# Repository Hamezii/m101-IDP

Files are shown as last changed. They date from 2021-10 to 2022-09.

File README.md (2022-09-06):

# CUED Integrated Design Project

- Integrated Design Project Project (10/2021 – 11/2021, 2 months)
- Robotics challenge organised by Cambridge University Engineering Department (CUED). The goal is to differentiate pure plastic blocks (blue) and blocks containing metal (red), then deliver the blocks to certain area (red and blue square areas).
- Our robot completed tasks and achieved 4th place among all 13 teams

<br>
Team name: TAIPEI101<br>

Team member:<br>
| name | Role |
| --- | --- |
| Derek Dong | Elec engineer, team leader |
| Laura Clapham | Elec engineer |
| Caleb	Chan | ME engineer|
| Ben Silva | ME engineer|
| Tom	Hill | Algorithm engineer|
| James	Lecomte | Algorithm engineer|

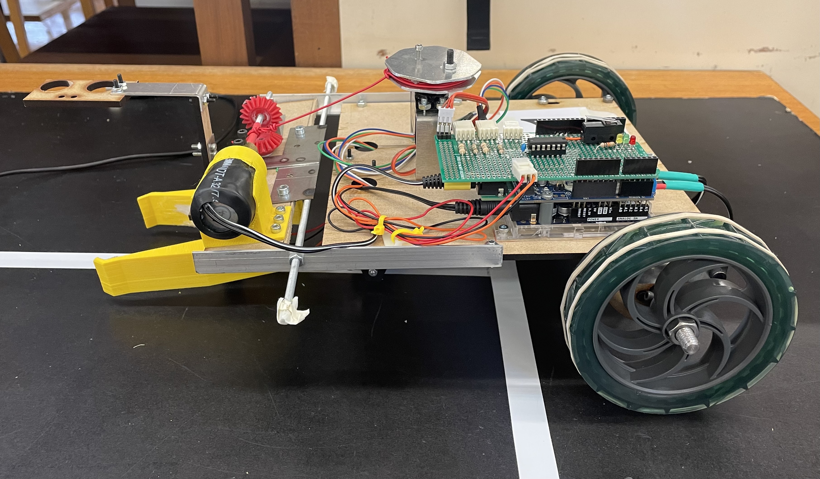
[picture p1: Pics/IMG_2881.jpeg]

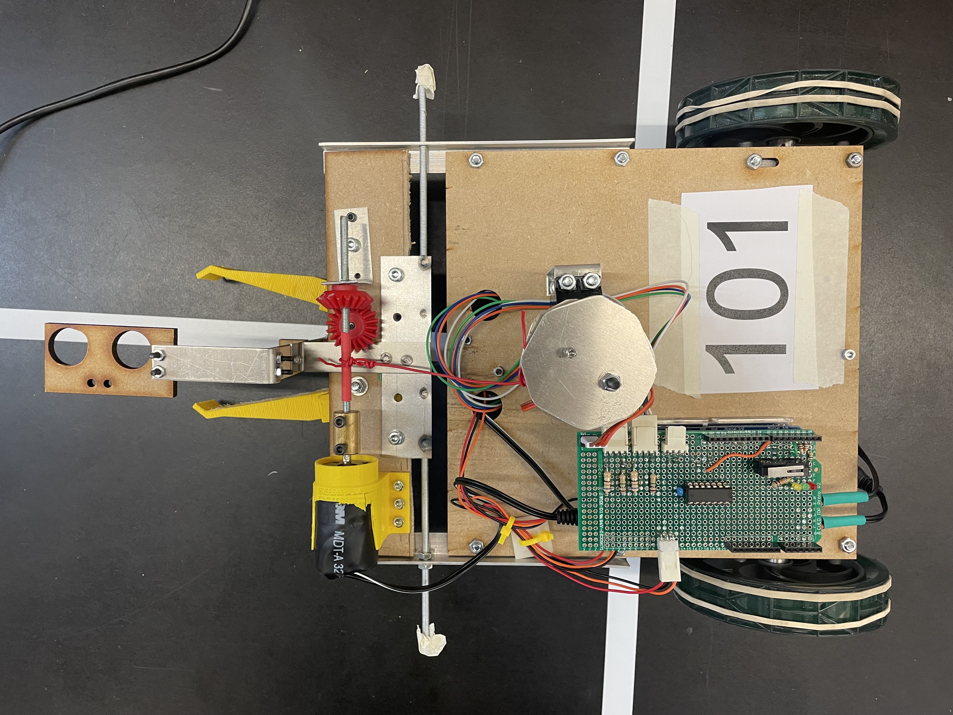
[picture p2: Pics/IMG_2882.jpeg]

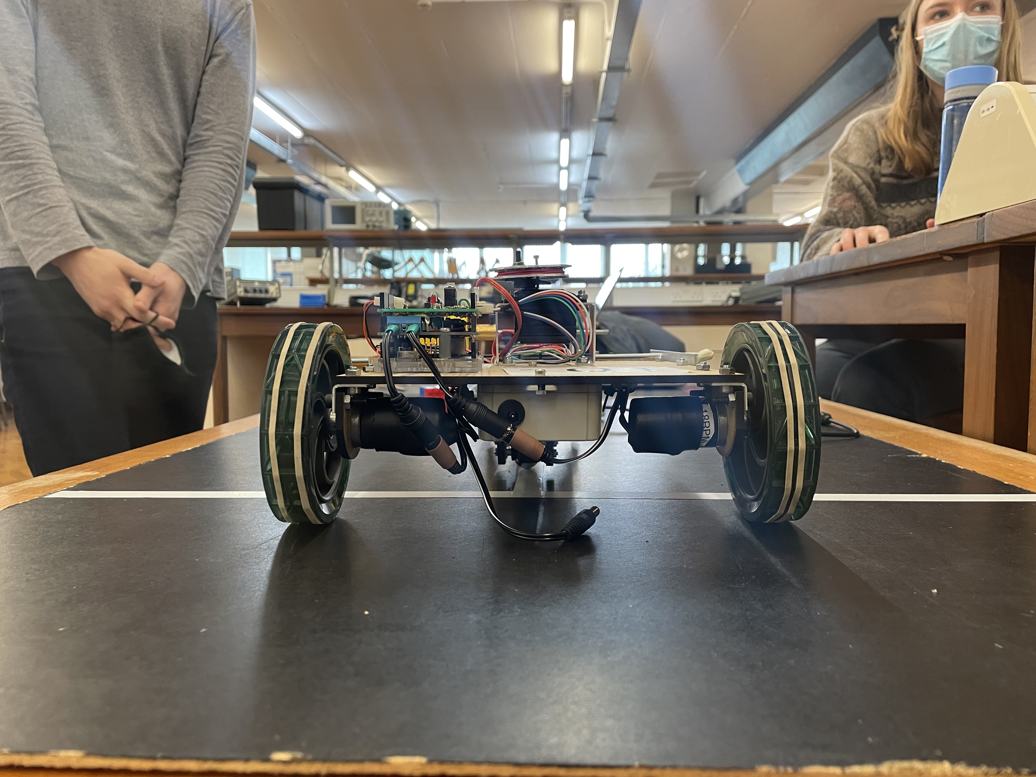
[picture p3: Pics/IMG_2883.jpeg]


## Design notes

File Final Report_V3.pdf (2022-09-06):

IDP REPORT – M101 | 1

### Department of Engineering

# TAIPEI 101 (M101)

# Final Report

Name | Crsid | Lab group
Laura S. Clapham | lsc43 | 43EM
Ben L.C. Silva | blcs2
Caleb C.C. Chan | cccc4 | 44EM
Tom Hill | th621
Derek J. Dong | jd976 | 45EM
James C-C. Lecomte | jccl4

### I. Outline

Design details

1. Overall Design Approach
2. Mechanics
a. Initial design of front section
b. Initial design of main chassis
c. Problems encountered and changes made after integrating
d. Driving
3. Electronics
a. Approach to design and testing
b. Metal Detection
c. Pathing (Line follower)
d. Block searching
4. Software

Reflections

1. Team Structure Review
2. Team Efficiency Review
3. Pathing & Block Searching Mechanism Review
4. Metal Detection system Review
5. Competitions Performance Review
a. Failure of 1st competition
b. Performance in final competition

Appendix

### II. Design details

### 1. Overall Design Approach

Our approach for the robot was to navigate to the collection zone using the line sensor, find the block using either the infrared distance sensor or ultrasound, clamp it in motorised arms, and then detect metal using a metal detector with a fixed position relative to the arms. We chose to use the line sensors as we thought computer vision was too difficult to implement in the time scale. This proved to be a good decision as one of our software team members fell ill and was forced to leave Cambridge, which would have made computer vision significantly harder to integrate.

We chose to use sensors to locate the block as we thought it would be more reliable than a mechanical system that attempted to sweep the entire collection zone at once. However, there was a lot of noise in the sensor signals which proved difficult to resolve and delayed the creation of a detection algorithm. This ultimately led to a redesign of our scanning process which was not fully implemented by the time of the competition. It is possible that by choosing a purely mechanical solution, we could have reduced the time needed to test and integrate, and therefore have been ready by the competition deadline. Our choice of arms was successfully implemented however, which provided good clearance over the ramp by elevating the block.

We decided to use a metal detector vs picking up the block with a magnet as we were unaware of the magnet’s availability during the initial planning stage, and when it became available, we did not stop to reconsider our previous choice. To ease integration with other components, we decided on a state-based program that was entirely modular. This eliminated the risk of a change effecting other parts of the program and was the right decision to make for a large project. However, it did make it slightly difficult for team members who had not encountered a state-based system to help check the code in the later stages of the project.

[Appendix D1: Whole system block diagram]

### 2. Mechanics

Initial design of front section

At first glance, we thought of hooping and dragging the block from the collection area back to the deliver area, as a less complicated mechanism would be required. However, when we inspected the competition table, we discovered that there is a small discontinuity going from the table surface to the ramp which might prevent the block being dragged over. [appendix M1] Therefore, we decided to lift the block to provide clearance above the ramp. To do this, we need a front section composing of the grabbing components which can be raised and lowered by a servo motor. We need a servo motor for this purpose because it can lock its position in order to keep the front section lifted. A spool of wire was constructed out of steel sheets and mdf, with the steel filed down to be roughly circular. We decided water jetting a steel circle was unnecessary and too slow.

Mounted on the front section is an 18 RPM motor, two grabber arms and a worm gear. After some prototyping with cardboard, we discovered turning one notch on the arm gears would require one full worm rotation. Turning 6 notches to close the arms would take 20 seconds with the 18 RPM motor which we decided is too slow. As a result, the worm gear is replaced with two helical gears which opens and closes within 1 second.

The main platform of the front section is 4mm MDF board laser cut to 200mm x 8mm. The brackets for the helical gears are made from steel sheets, and the front section is connected to the main section by a steel plate spot-welded to a studding and bolted to the front section. The arms were prototyped in bent steel, and later changed to 3D printed.

Initial design of main chassis [appendix M2: CAD of Robot] [appendix M3: Picture of Robot]

As the arms will continuously grab the block and be lifted until the robot reaches the collection area, there is no need for a place on the chassis to store the block. Therefore, in order to keep manufacturing process as simple as possible and high accessibility to components, we went with a flat platform design. The chassis is made of 4mm MDF sheet laser cut to 200mm x 200mm.

We discovered it would be difficult to steer the robot using 4 wheels. Therefore, we decided to use a 3-wheel system, with two motorised wheels and a ball caster as the third support. This allows us to steer the robot by just giving the motors different angular velocity and let the ball caster swing left and right. The 4” wheels are chosen for two reasons: a) to maximise speed (40RPM x 4” x π = 12.8 m/min and b) to keep the chassis high off the ground enough so it does not get stuck on the edge of the ramp and the bridge. Although this raises the centre of mass, which could affect stability, we decided to go ahead as we believe our wheelbase is long enough to prevent the robot from tipping over. The ball caster is mounted onto the chassis with a long arm in order to keep the chassis levelled.

The servo motor is mounted on the main chassis, and it would pull a string attached to the front section, which would be pivoted against the front of the main chassis. Shelves are placed at the rear of the chassis to place the Arduino boards and circuit boards. The battery is mounted towards the rear of the chassis on the underside to offset the moment created by the front section and maximise space for electronics. Most of the mounts will be fabricated by bending aluminium sheets into the right shapes. The motor mount was originally 3D printed. However, given the wire heat-shrinked onto the motor casing gives it a lot of irregularities, the 3D printed mount could not grip the motor properly. So, we switched to using a MDF board cut-out which is mounted to the screw plate of the motor and the main chassis though an aluminium angle.

Problems encountered and changes made after integrating

When we first assembled the robot and tested the line following algorithm, we discovered some major problems.

First, due to wear and tear of the motors from previous years, the power and torque output by the 40RPM motors are not balanced, meaning 1 side of the robot has more driving force acting on it than the other side, causing the robot to always drift. The bigger problem is that the side with less power could not climb up the ramp, causing the robot to rotate up the ramp. To solve this, we switched out the 40RPM motors for 18RPM motors which are in slightly better condition and capable of producing more torque. As expected, the change turns out to be the right one.

With the 18RPM motor switched out, we had to use the 40RPM motor to drive the grabber arms, which caused the second problem. The 40RPM motor does not produce enough torque for the grabber arm to grip the block firm enough. As a result, we had to put something on the surface of the grabber arm to increase friction. We have tried sandpaper, heat shrink and rubber bands, at the end we went with spreading an even layer of hot-melt adhesive on the surface. Although it is not an elegant solution, it gives us just enough grip to transport the block.

As we were testing the line following algorithm, it was discovered that the robot was slightly understeering. This caused issues in line detection and pathing, as the algorithms worked off the assumption that the point of rotation lied on the driving wheel axes. To fix this we shorten the front section to bring the centre of mass towards the rear to allow easier steering.

### 3. Electronics

[Appendix E1: Overall schematic diagram] & [Appendix E2: Overall layout]

Approach to design and testing

There were three main tasks for the electronics team: metal detection, line following and block searching. Originally, we split tasks among the team and worked on them separately. This approach had its advantages, like easily being able to work on the project at home and getting two tasks done at once, but eventually we realised that it was more effective to work together on the same task. This meant we could use different perspectives and ensure that each other moved on when something wasn’t working instead of obsessing over the same strategy.

The three main tasks remained almost completely isolated from each other throughout the project meaning we could easily ensure that each aspect was working properly before we used them all together. LT Spice was used to model behaviour of systems and to optimise values of components and the output signals were measured using a PicoScope and the Arduino.

The electronics team had to work with the mechanics and software teams closely. For example, the design of the metal detector affected its location on the robot and whether it would have to move up and down using a servo. The output of the metal detector had to be interpreted and processed by the software team. A rolling average algorithm was used to clean the signal and the result taken by the metal detector would have to change the state of the robot.

Metal detection

The metal detector uses an AD22151 magnetic field sensor that contains a hall effect sensor and amplifier circuit. It gives out a high voltage when the magnetic field strength is over a certain value and otherwise a low voltage. A magnet is placed above the sensor at a distance that gives a low value when there is no metal in between it and the sensor but a high value when the block is placed on top of the sensor. The circuit was soldered onto its own board and placed in between the grabber arms. As the robot drove up to the block, the block would be pushed onto the breakout board containing a hall effect sensor.

The magnetic field sensor was a late revelation as the solution for the vast majority of the project was to use a coil. The circuit would have used the fact that the inductance of a coil increases when in the presence of ferrous metal. The inductor was used in a tank circuit with a capacitor. When the inductance increases the charge collected on the capacitor, and so the voltage over the capacitor, increased and could be measured. The reason this was changed is explained in the reflections section.

Pathing (Line follower)

For pathing, we wanted to allow the robot to be aware of its position on the table, and to do so we want line sensors to detect lines. We want the robot to be able to follow lines and detect perpendicular lines it comes across, so we designed a system to satisfy both criteria. We put two line-sensors on the front of the robot since it is the minimum amount needed to gather enough information.

The line follower circuit includes an OPB704 line sensor which uses an LED, emitting IR light, and a phototransistor. When on the line a low voltage is output and when off the line a high voltage is output. This signal enters a SN7414N Hex Schmitt inverter before being input to the Arduino for use in the line following program.

The accurate position of two sensors were carefully considered. The main problem was that the distance between sensors and the ground changed when the robot going up or down on the ramp, and line sensors only work in a certain range of distance. We managed to find out that the rear of the front wheel is a good position, and specific distance was determined by several experiments.

Block searching

The final plan was to mount the ultrasonic sensor in front of the robot facing downwards and for the robot to scan the entire box by rotating to scan the entire width then moving forward and scanning the next width and so on. The failure of this aspect is explored further in the reflections section.

### 4. Software

[Appendix S1: Flowchart of software]

The basic of our software design is state-driven: we used Finite State Machine to determine robot behaviour
s. All sensor inputs are converted to a rolling average to decrease the noise.

Pathing algorithm is based on 2 line sensors. Data from the line sensor is used to correct the direction of the robot by changing the velocity of the left and right wheel motors separately in a negative feedback loop. When one sensor circuit detected a white line the robot would know that its path was deviating too far to the other side and so it would turn in the opposite direction until this was corrected.

The program could remember when a horizontal line was crossed (detected when Arduino receives high signals from both sensor circuits). This allowed the robot to know which state to enter at which time, for example it would know when it had reached the collection box and so would know when to start the grabbing cycle.

### III. Reflections

### 1. Team Structure Review

Our team have one team leader and 3 sub-teams (ME, Elec, Software). We used Slack to communicate, GitHub to share progress and Gantt chart to track deadlines.

3 sub-teams structure can make sure that every member has a clear role, which is quite manageable and normally increases team productivity. However, in a small project like IDP, some drawbacks are shown. First, this structure reduces communication between sub-teams, which means lack of information flow. For example, some of our team members did not know much about software designs. Before the first competition, all the members who knew how the software works happened to be absent until 2 minutes before the competition, and the three remaining members couldn’t even start the robots. This resulted in us not having time to test the robot before the competition and thus failing in it. Second, it also leads to some under-utilisation of human resources (e.g. the software cannot be tested until the overall robot has been built). Potential improvement includes having more team meeting to help communicate and educating other sub-teams on how stuff works to allow them to know the overall graph.

Having a clear team leader can lead to a high team productivity and can ensure the decisiveness of the team in case of disagreement. However, the advantages highly depend on the leader: When the leader is not good at managing or cannot devote sufficient effort to managing, the team productivity decreases dramatically (this happened in the project).

### 2. Team Efficiency Review

From the team leader’s point of view, the team M101 has good productivity, but it can still be improved by several measures:

- Avoid schedule mistakes (e.g. Dyson centre opening hours)
- Set specific tasks for each lab session instead of setting a vague goal of “do this by that time”. For each phase rather than talking about what to do in general (e.g. set a deadline as “implement line-following before 16 Oct” “finish final chassis cut and start to build final circuit on it before 2 Nov” instead of “we should finish all designs before 10 Oct” “We should combine all parts to get a complete robot before 15 Oct”. They can be good guidelines but not suitable deadlines.
- Consider team focus carefully. Vital tasks should be figured out and focused on in advance so that team productivity can be fully used to gain the most benefits.
- Report progress to teach other sub teams about how to get your finished work integrated so when some member becomes unavailable during the project (which happened to us), other sub team members can substitute and help with balancing workload.

### 3. Pathing & Block Searching Mechanism Review

Computer vision & line-following

Computer vision was seriously considered along with line-following as path-designing method at the beginning of the project. We considered it as a powerful tool but decided that this would not be necessary, since using it would be an over-engineered solution that has many failure points and would take too long to develop and is likely to be unreliable. It is too dependent on factors like the brightness level of the room and shadows cast on the table, etc.

Block searching

Implementing a block searching mechanism was the most challenging aspect of the project; there were many issues with the distance sensors that were not apparent at the start. When the block surface is not directly normal to the sensor the readings given are inaccurate and inconsistent. Therefore, the original design where an ultrasonic sensor would be placed at the front of the robot facing horizontally was problematic. Mounting the ultrasonic sensor on an antenna-like structure so that it points down solved this issue. This unfortunately was only sorted late into the project so it was difficult for the software team, who were often unable to attend, to code a way for the robot to scan the box. It became apparent that it was going to be almost impossible to finish the block finding system in time for the final competition so we had to make the decision to leave it out and focus on other things so we could at least secure 30 points.

Metal detection system review

One of the biggest major changes in the design of the robot was the switch from a inductor coil-based system to detect metal to a hall effect sensor at 3 weeks into the project. This was the correct decision to make as previous detectors using the coil were extremely noisy and unreliable, however it was a difficult decision to make as considerable amounts of time had been spent trying to make them work. With hindsight the decision should have been made a long time before but the small advances with the detector coils made it seem as though a breakthrough was always near. The main problems with using the coils were that they were insensitive and so struggled to detect the small amount of steel within the block. It was also time consuming to make different coils to test and optimize the components used in the circuit.

Competition's performance review

- Failure of 1st competition

Our expectation before the 1st competition was to reach the other side but not to collect or sort block. The robot had been capable of achieving this for several days, but the day before the competition we integrated the grabbing section onto the main chassis. We found in testing that this made the robot too heavy to climb up the ramp, so we knew that the front section needed to be removed for the competition. This meant it was impossible to pick up a block, but possible to cross the ramp.

However, during our testing of the robot, it seems that the left motor axle had come loose from the casing. This was likely due to a combination of historic wear and tear, and stressing the motor by having too heavy a weight for its torque limit. As a result, during the competition, in a configuration that had previously worked, the robot was unable to climb the ramp. It veered to the left and either ran off the ramp or toppled over. We had not been able to test the robot immediately before the competition, as only 3 members had arrived in time to test it, and none of them knew how the software operated. This revealed a flaw in our team management that we sought to improve before the final competition.

Coming out of the competition we had several priorities: to reduce the weight to torque ratio to an acceptable level, and to integrate the metal detector and detection algorithm. We solved the weight problem by swapping the motors as detailed in the mechanical section. We also ensured for the final competition that more people had a basic understanding of the software, and that we stopped working on the robot in plenty of time before the competition, in a state that we could test and see work.

- Performance in final competition

The day before the competition we had tested all the mechanical and electrical systems working together and all that was left to do was to integrate the software to create a scanning cycle to locate blocks. Our minimum expectation was that we could pick up the first block, as it would be placed in the same place every time, and we were hoping to be able to locate other blocks using the cycle.

However, on the day of the competition, our software team was not able to attend until an hour and a half before the competition. As more of the team had knowledge of the software vs the first competition, we were still able to test the robot and debug the code, but we were unable to create the new software needed for the scanning cycle. Therefore, we were unable to achieve more than our minimum expectation.

We did quite well in the final competition and the performance was exactly what we expected before competition: our robot managed to get the first block and correctly told the difference between metal and plastic. Compared with the first competition, our strategies changed: We still did R&D on the morning before the final competition, but each progress made was archived and ensured that it could be easily replicated. With an hour to go, we stopped development to concentrate on the competition and ensure a consistent, predictable performance in the competition.

### Appendix

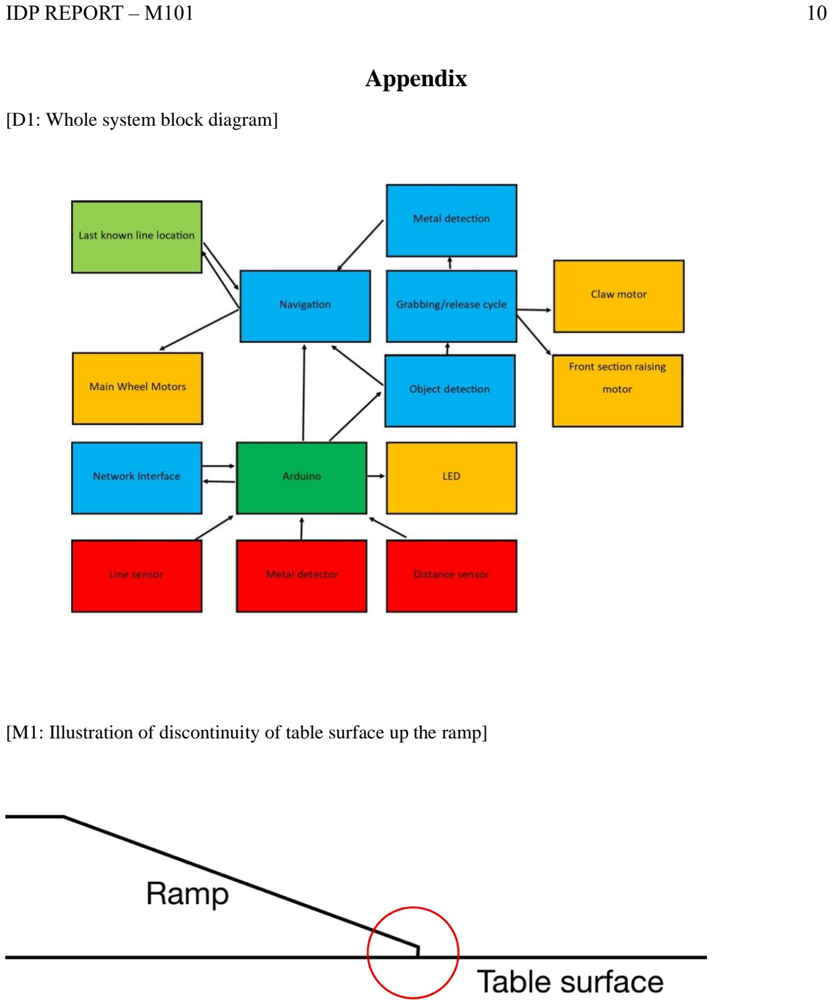
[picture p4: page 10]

[D1: Whole system block diagram]

[M1: Illustration of discontinuity of table surface up the ramp]

[M2: CAD of robot]

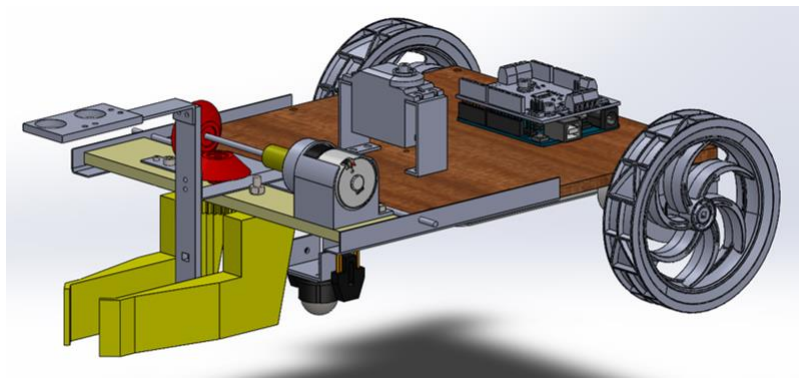
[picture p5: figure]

[M3: Assembled Robot]

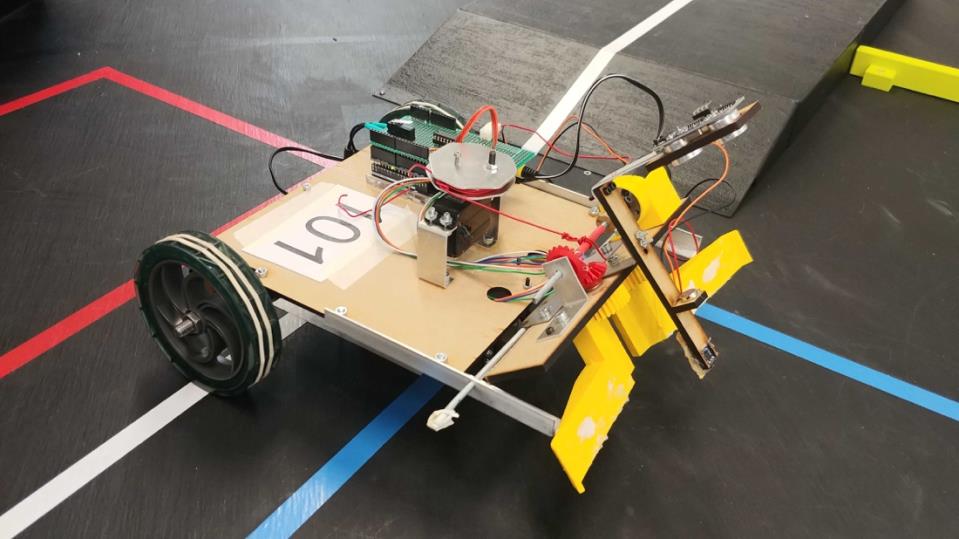
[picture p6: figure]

[M4: Torque

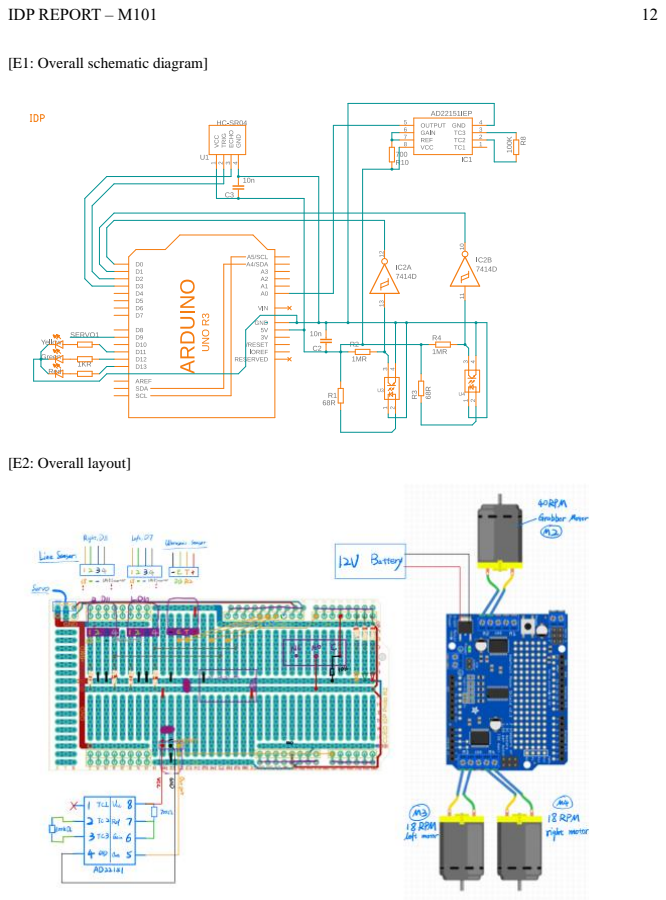
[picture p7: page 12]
[E2: Overall layout]

[E1: Overall schematic diagram]

IDP REPORT

– M101 | 13

[S1: Flowchart of software

]

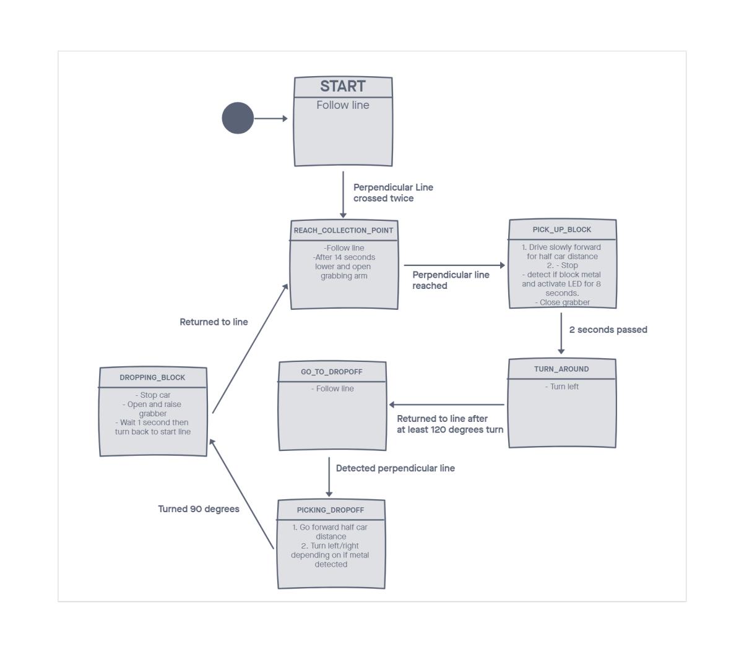
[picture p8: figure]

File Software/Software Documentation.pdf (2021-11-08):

# Software Documentation

James Lecomte jccl4 + Tom Hill th621

## CODE

Permalink to Github repo:

https://github.com/Hamezii/m101-IDP/blob/80b2492b2193943c890ced5abd1d3d18f783d01f/Software/IDPmain/IDPmain.ino

## STRATEGY

ALGORITHM AND STATE
For the robot to keep track of its location and its current place in its behaviour algorithm, we implemented a Finite State Machine into the program. This allowed us to explicitly separate the robot behaviour during the different stages of execution into their own state. This also allowed easy

## EXECUTION

SYSTEM DIAGRAM

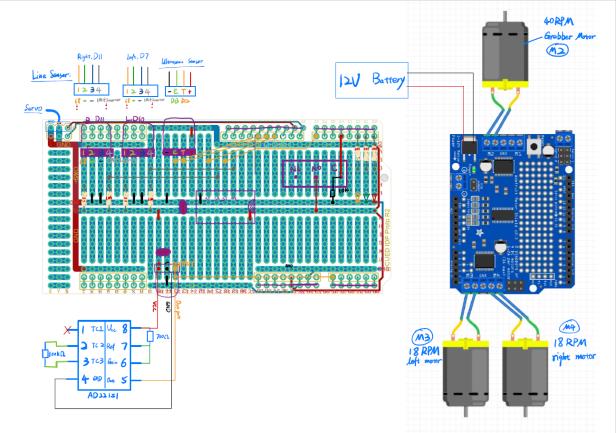
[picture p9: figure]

MAIN STRUCTURE
The program consists of subroutines organised using a state machine that enable navigation with line following, object detection with the ultrasonic sensor, metal detection, object grabbing and lifting, placing objects into the appropriate boxes, etc.

The behaviour of the robot at any given time is driven by the FSM; at any arbitrary time-step, using a combination of current state and inputs into the Arduino, the robot will modify its state and behaviour, calling subroutines to do so.

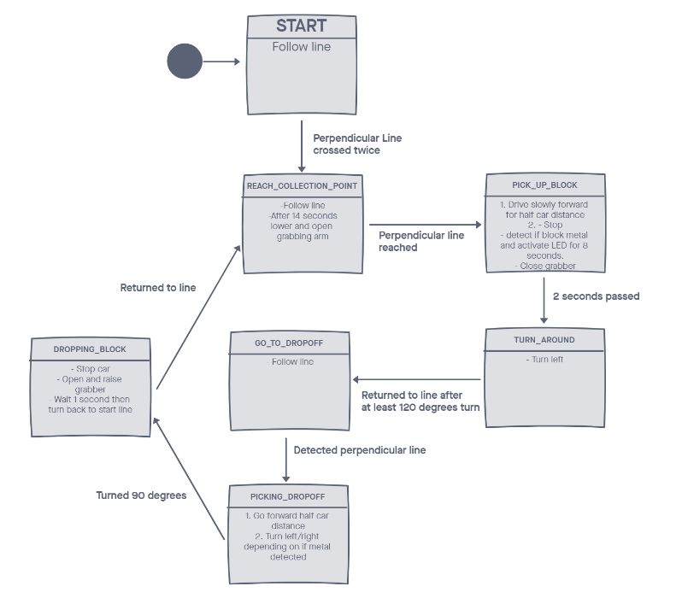
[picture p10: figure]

2

STATE DIAGRAM

PARALLEL PROCESSES
We wanted to allow continuous robot output behaviour and state management in parallel with continuous sensor readings (for running averages, see below). To do this we made sure subroutines don’t block the execution of the program by running for a non-trivial period, for example by using delays in a for loop for a continuous motion, as this essentially blinds the robot during its execution. The FSMcentric design allowed for continuous behaviour over multiple program cycles.

DETECTING PERPENDICULAR LINES
When following a line, if both line sensors read high it can be assumed that the robot has crossed onto a line perpendicular to its direction of movement. In practice, this can be used to detect an edge of the different boxed zones on the table, as well as the point at which two lines intersect.

SENSING
To ensure accurate readings from the different sensors on the robot, we made sure to eliminate noise and false readings by implementing a running average for each sensor. We read the value of each sensor every program loop and pushed it into a Queue-like RunningAverage abstract data type, taking the average of the values in the queue when polling sensors for conditional logic.

Using trial-and-error, we found that a good value for size of the running average Queues was 4, as too small would allow a single noisy reading to disrupt the mean reading and too large would cause the robot to respond too slowly to large discontinuous changes in read value i.e. when line sensors pass over a line.

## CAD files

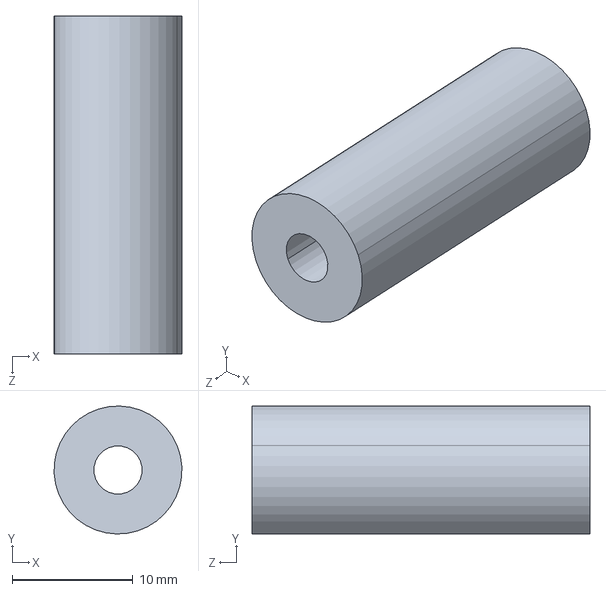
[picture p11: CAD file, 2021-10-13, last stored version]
ME/Gear Drive.SLDASM
10.6 x 10.6 x 28.0 mm

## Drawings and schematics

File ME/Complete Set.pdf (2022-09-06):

13 | 11 | 12 | 2 | 19

23

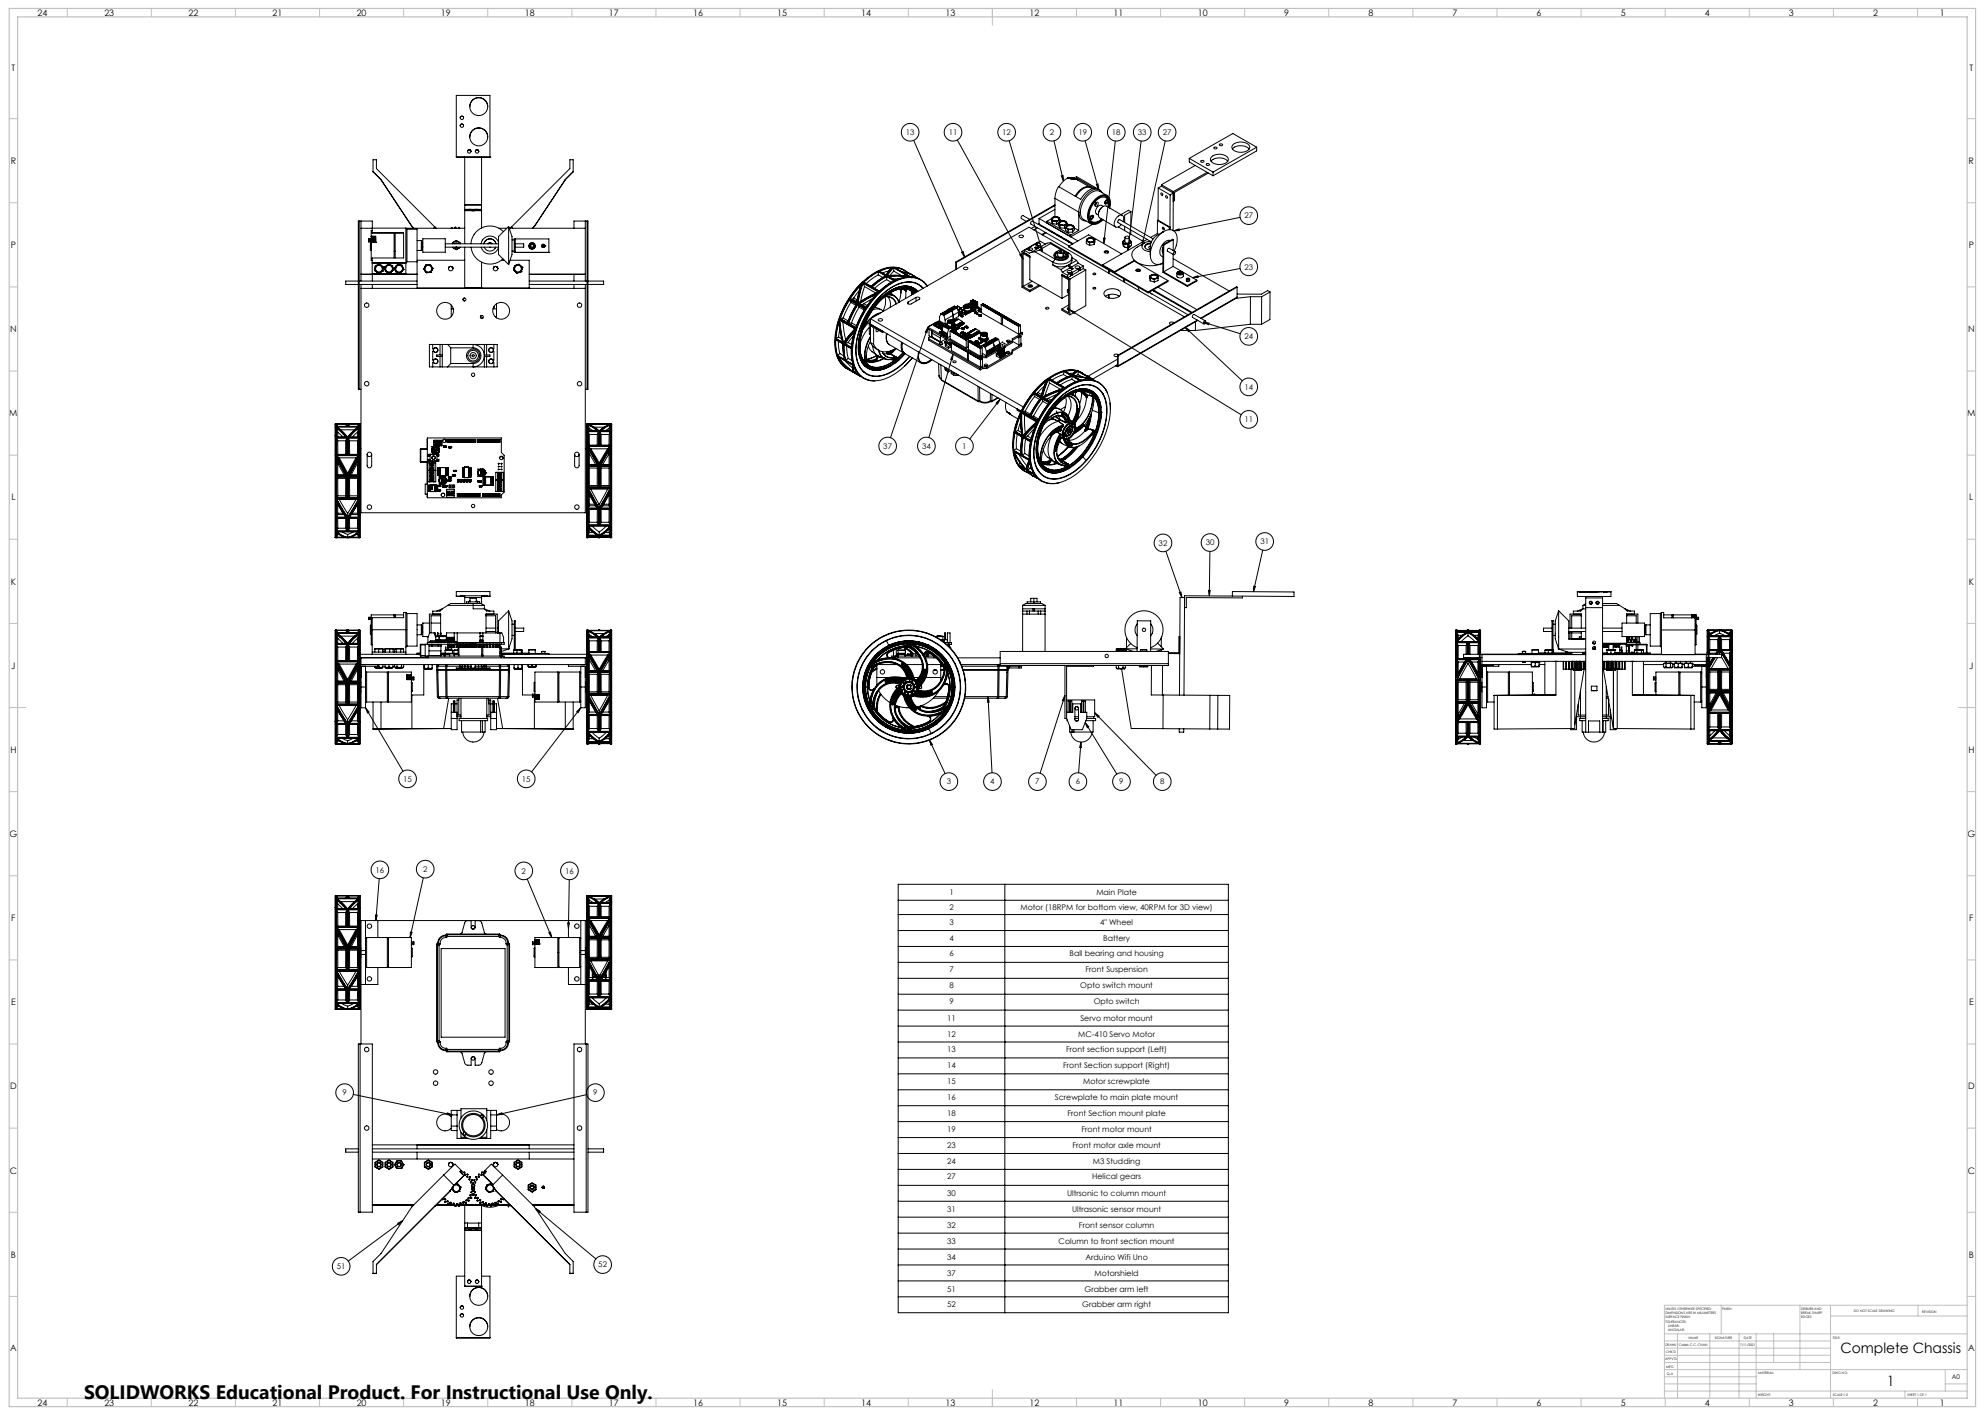
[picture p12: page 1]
FINISH:; DEBURR AND; BREAK SHARP EDGES; DO NOT SCALE DRAWING; REVISION; SCALE:1:2; SHEET 1 OF 1; WEIGHT:

1 | Main Plate
2 | Motor (18RPM for bottom view, 40RPM for 3D view)
3 | 4" Wheel
4 | Battery
6 | Ball bearing and housing
7 | Front Suspension
8 | Opto switch mount
9 | Opto switch
11 | Servo motor mount
12 | MC-410 Servo Motor
13 | Front section support (Left)
14 | Front Section support (Right)
15 | Motor screwplate
16 | Screwplate to main plate mount
18 | Front Section mount plate
19 | Front motor mount
23 | Front motor axle mount
24 | M3 Studding
27 | Helical gears
30 | Ultrsonic to column mount
31 | Ultrasonic sensor mount
32 | Front sensor column
33 | Column to front section mount
34 | Arduino Wifi Uno
37 | Motorshield
51 | Grabber arm left
52 | Grabber arm right

UNLESS OTHERWISE SPECIFIED:
DIMENSIONS ARE IN MILLIMETERS
SURFACE FINISH:
TOLERANCES:
LINEAR:
ANGULAR:

NAME | SIGNATURE | DATE | | | | TITLE: Complete Chassis

SOLIDWORKS Educational Product. For Instructional Use Only.

DRAWN | Caleb C.C. CHAN | | 7/11/2021
CHK'D
APPV'D
MFG
Q.A | | | | MATERIAL: | DWG NO. | A0

49.50 ².50

0

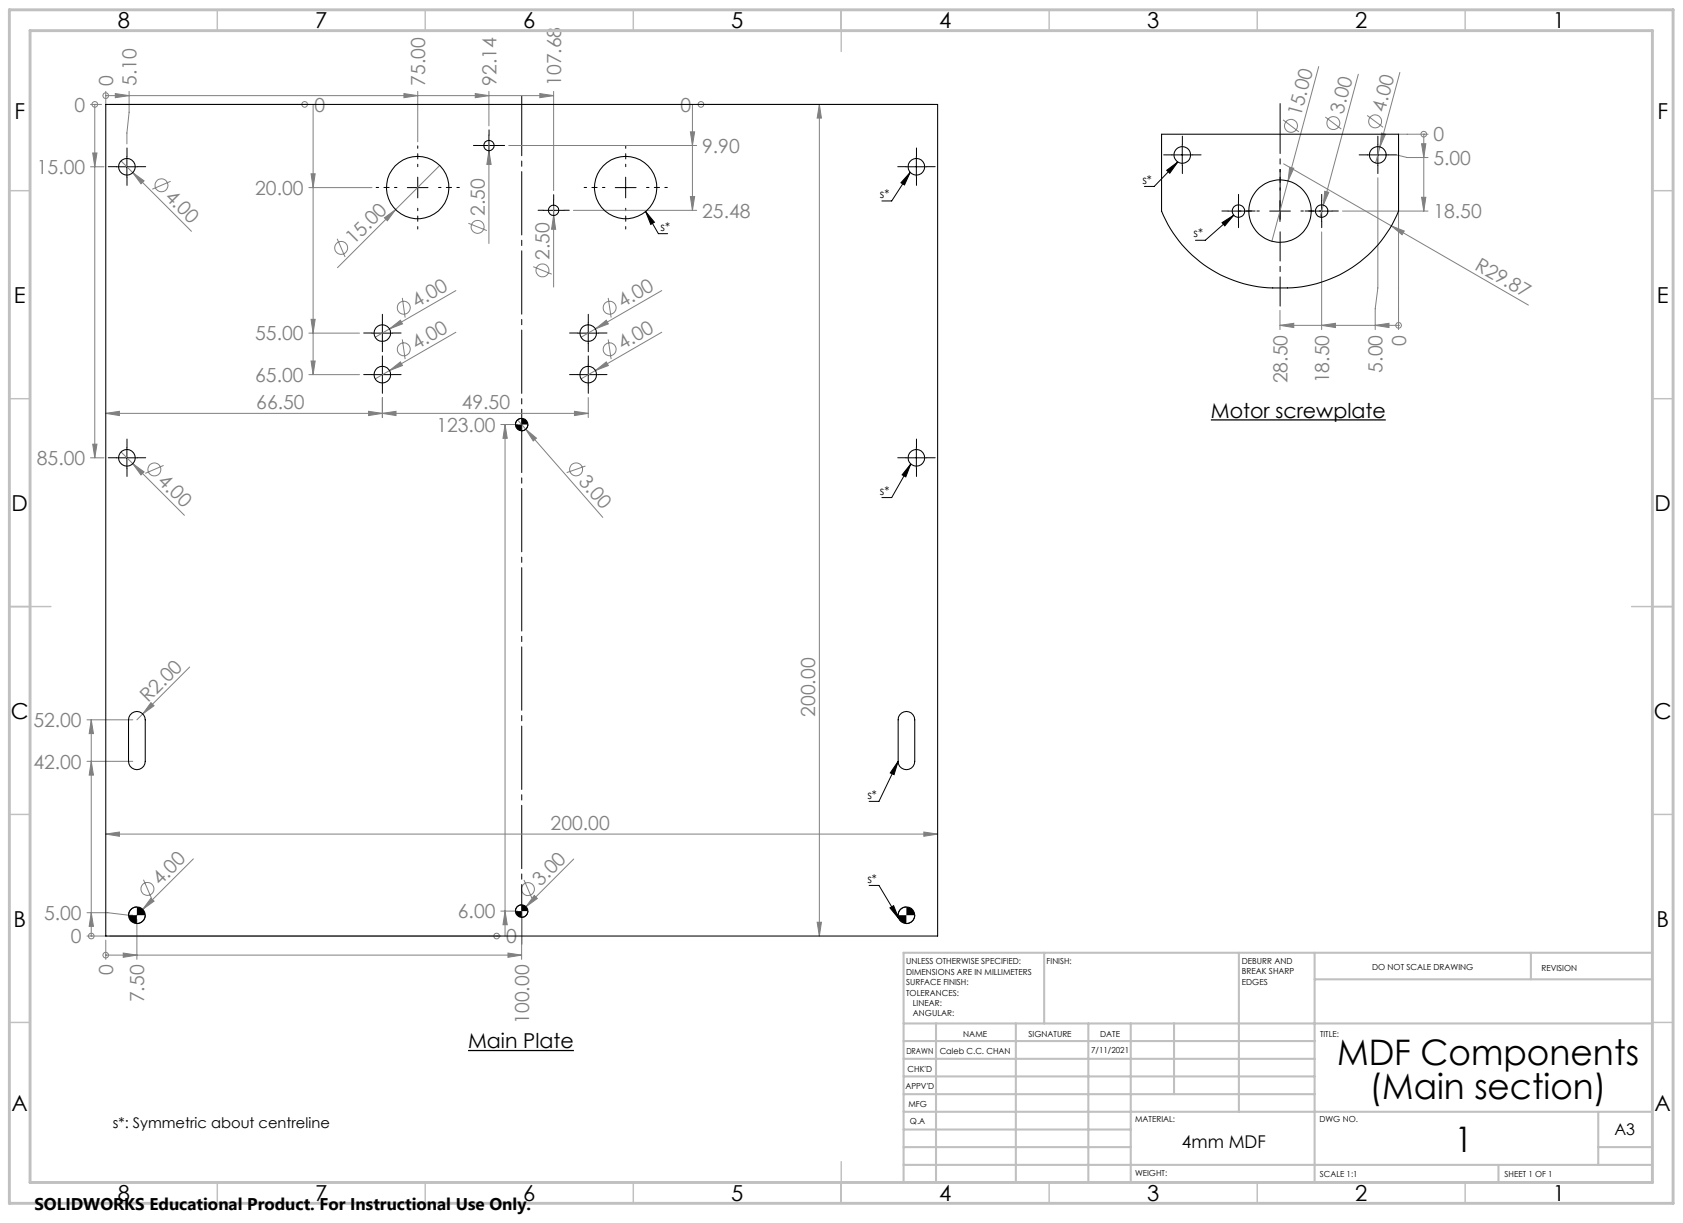
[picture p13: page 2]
Main Plate; Motor screwplate; FINISH:; DEBURR AND; BREAK SHARP EDGES; DO NOT SCALE DRAWING; REVISION

UNLESS OTHERWISE SPECIFIED:
DIMENSIONS ARE IN MILLIMETERS
SURFACE FINISH:
TOLERANCES:
LINEAR:
ANGULAR:

NAME | SIGNATURE | DATE | | | TITLE: MDF Components (Main section)

DRAWN | Caleb C.C. CHAN | | 7/11/2021
CHK'D
APPV'D
MFG

s*: Symmetric about centreline

A3 4mm MDF

SCALE 1:1 | SHEET 1 OF 1

E | E
F | F

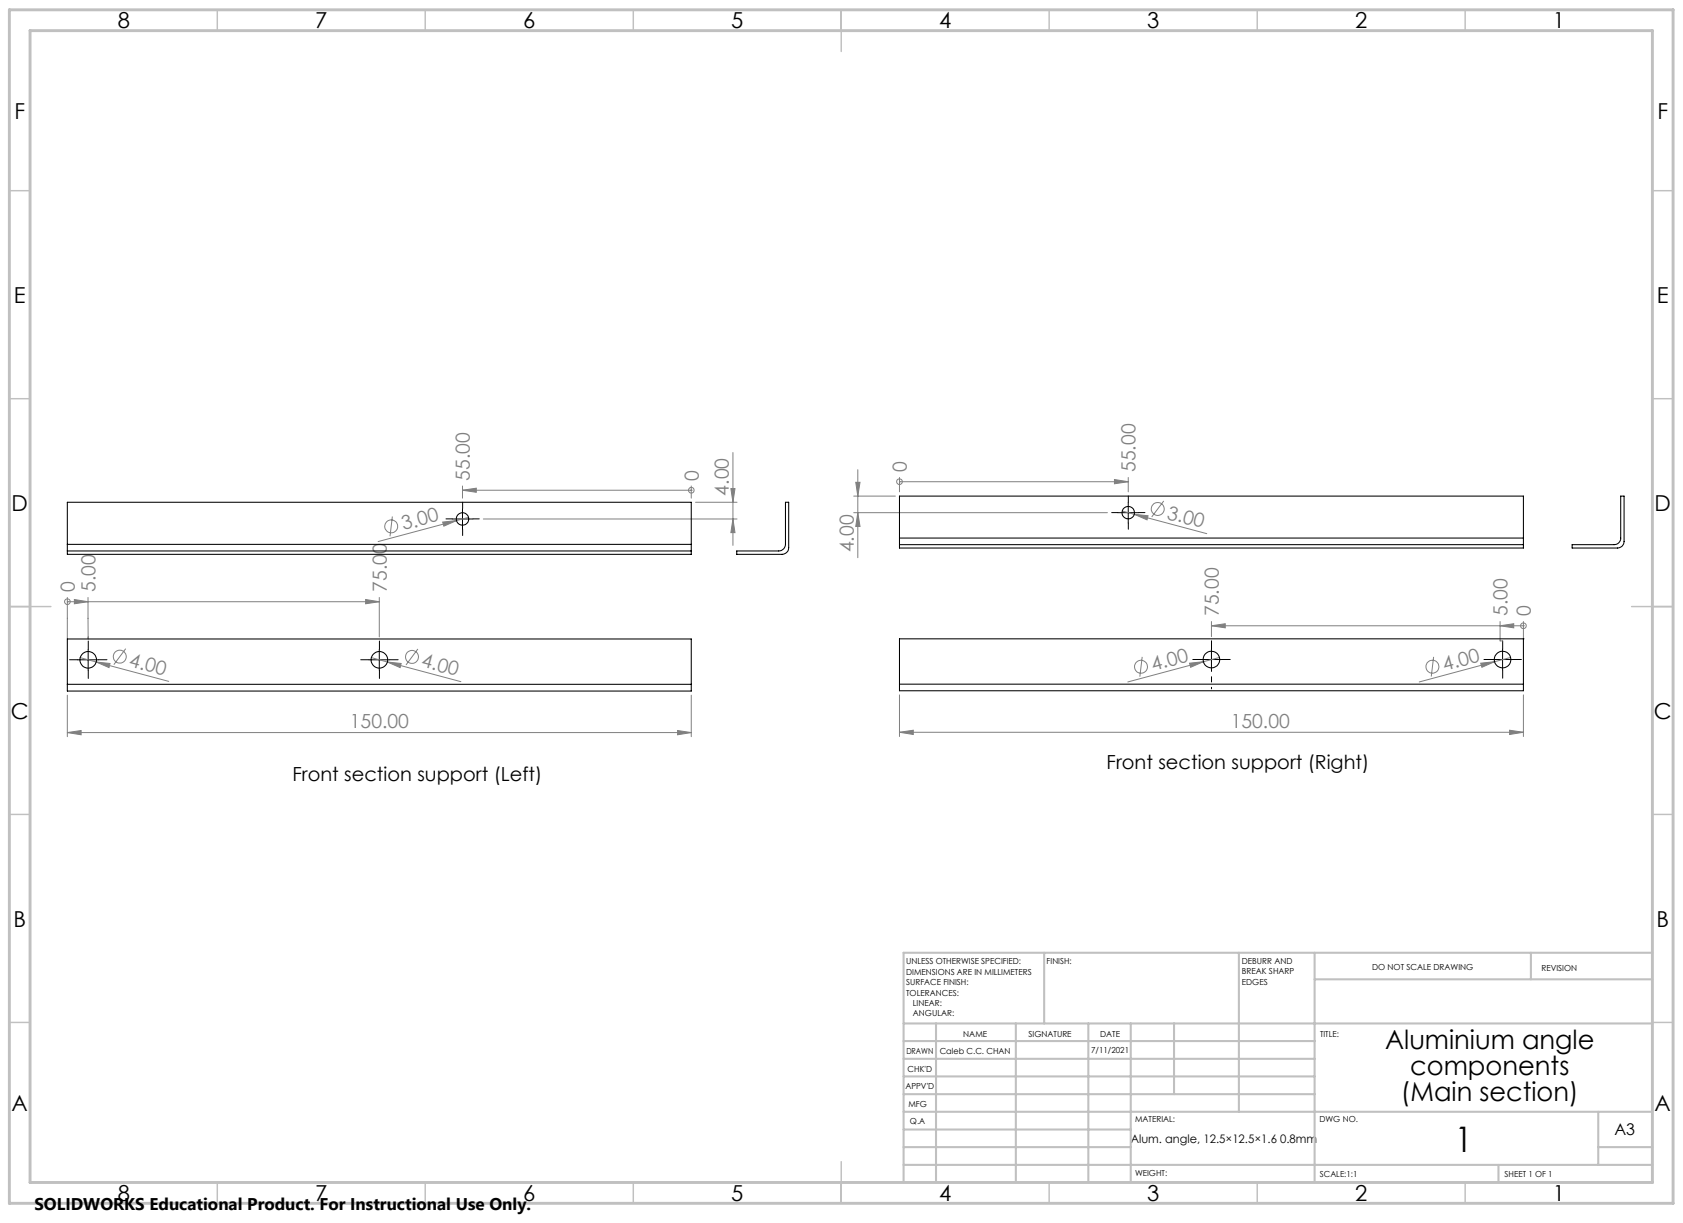
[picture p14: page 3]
FINISH:; DEBURR AND; BREAK SHARP EDGES; DO NOT SCALE DRAWING; REVISION

Front section support (Right)

Front section support (Left)

UNLESS OTHERWISE SPECIFIED:
DIMENSIONS ARE IN MILLIMETERS
SURFACE FINISH:
TOLERANCES:
LINEAR:
ANGULAR:

NAME | SIGNATURE | DATE | | | Aluminium angle TITLE: components (Main section)

DRAWN | Caleb C.C. CHAN | | 7/11/2021
CHK'D
APPV'D
MFG

A3 Alum. angle, 12.5×12.5×1.6 0.8mm

SCALE:1:1 | SHEET 1 OF 1

27.00

## UP 90 deg UP 90 deg

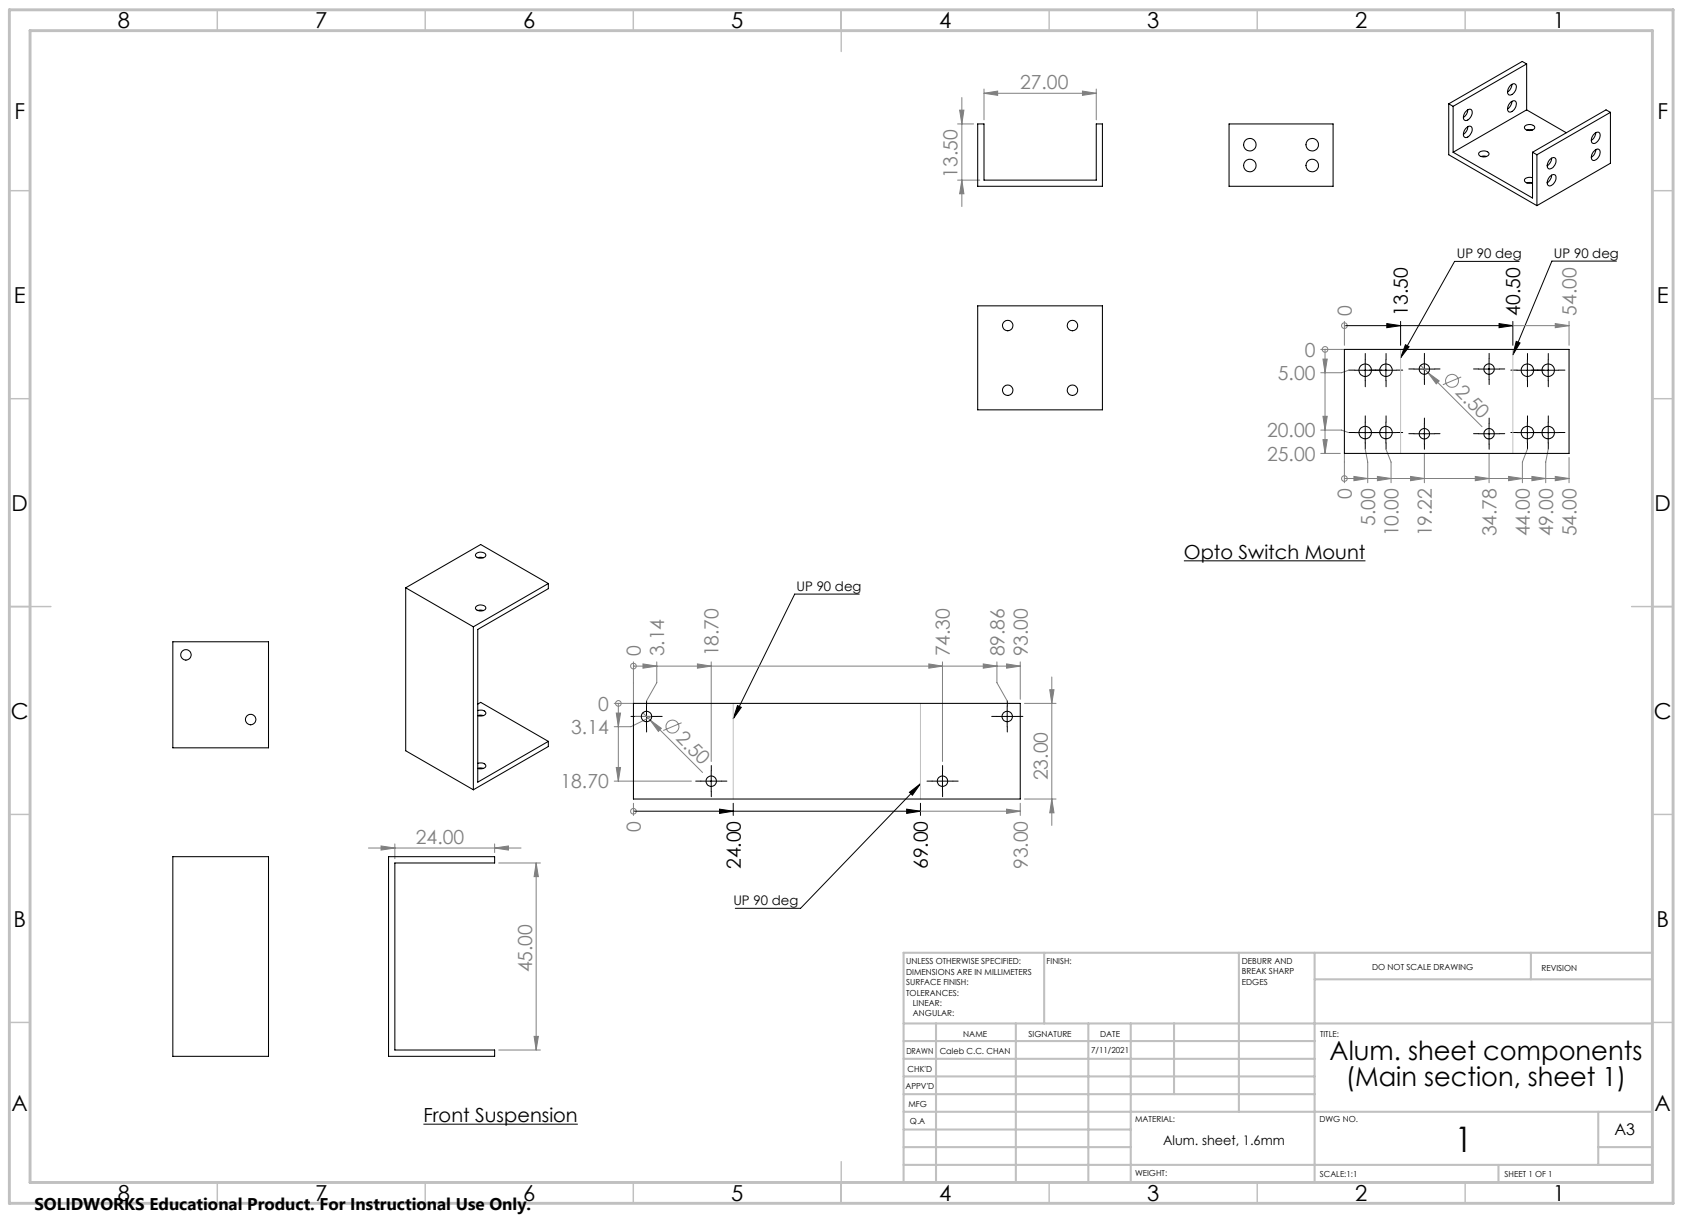
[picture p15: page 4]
UP 90 deg; Front Suspension A; FINISH:; DEBURR AND; BREAK SHARP EDGES; DO NOT SCALE DRAWING; REVISION

Opto Switch Mount

UNLESS OTHERWISE SPECIFIED:
DIMENSIONS ARE IN MILLIMETERS
SURFACE FINISH:
TOLERANCES:
LINEAR:
ANGULAR:

NAME | SIGNATURE | DATE | | TITLE: Alum. sheet components (Main section, sheet 1)

DRAWN | Caleb C.C. CHAN | | 7/11/2021
CHK'D
APPV'D
MFG

A3 Alum. sheet, 1.6mm

15.00
E | E

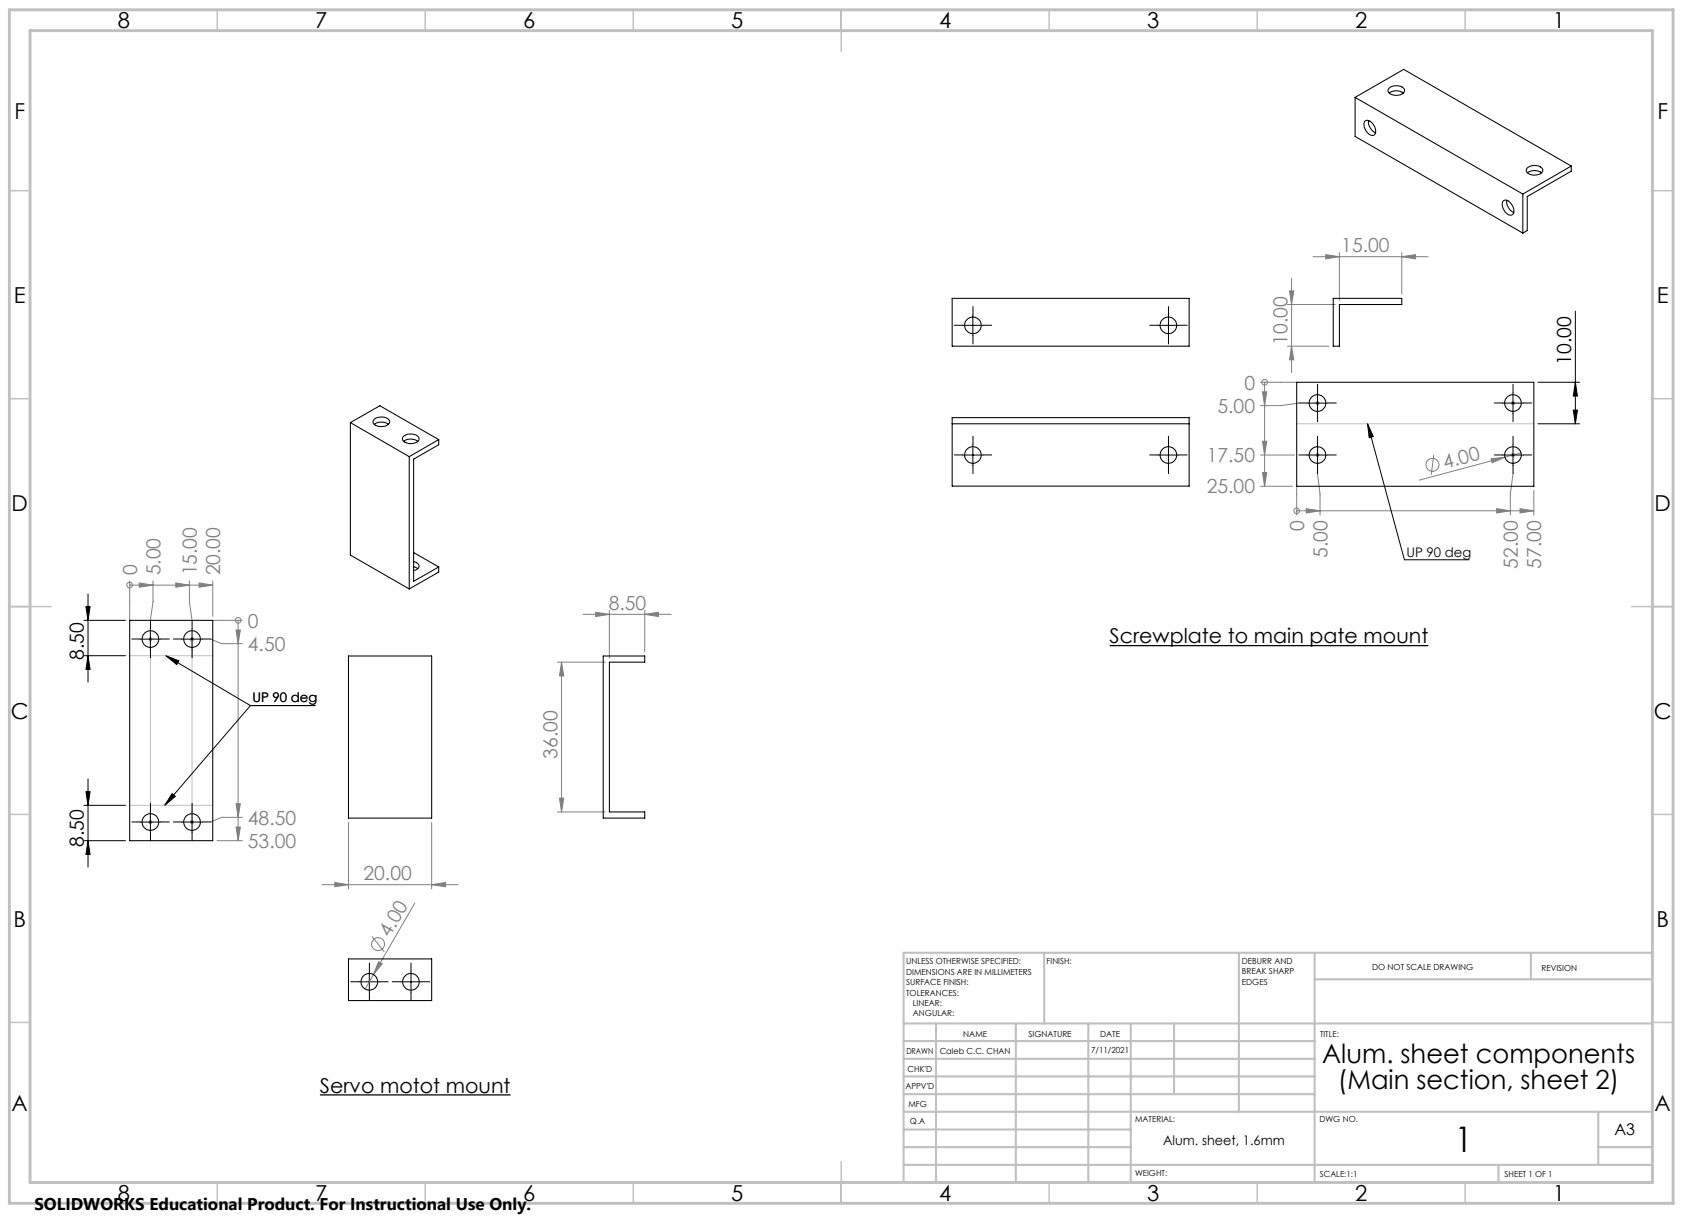
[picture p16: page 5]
UP 90 deg; FINISH:; DEBURR AND; BREAK SHARP EDGES; DO NOT SCALE DRAWING; REVISION

Screwplate to main pate mount

UNLESS OTHERWISE SPECIFIED:
DIMENSIONS ARE IN MILLIMETERS
SURFACE FINISH:
TOLERANCES:
LINEAR:
ANGULAR:

NAME | SIGNATURE | DATE | | TITLE: Alum. sheet components (Main section, sheet 2)

DRAWN | Caleb C.C. CHAN | | 7/11/2021
CHK'D
APPV'D
MFG

Servo motot mount

A3 Alum. sheet, 1.6mm

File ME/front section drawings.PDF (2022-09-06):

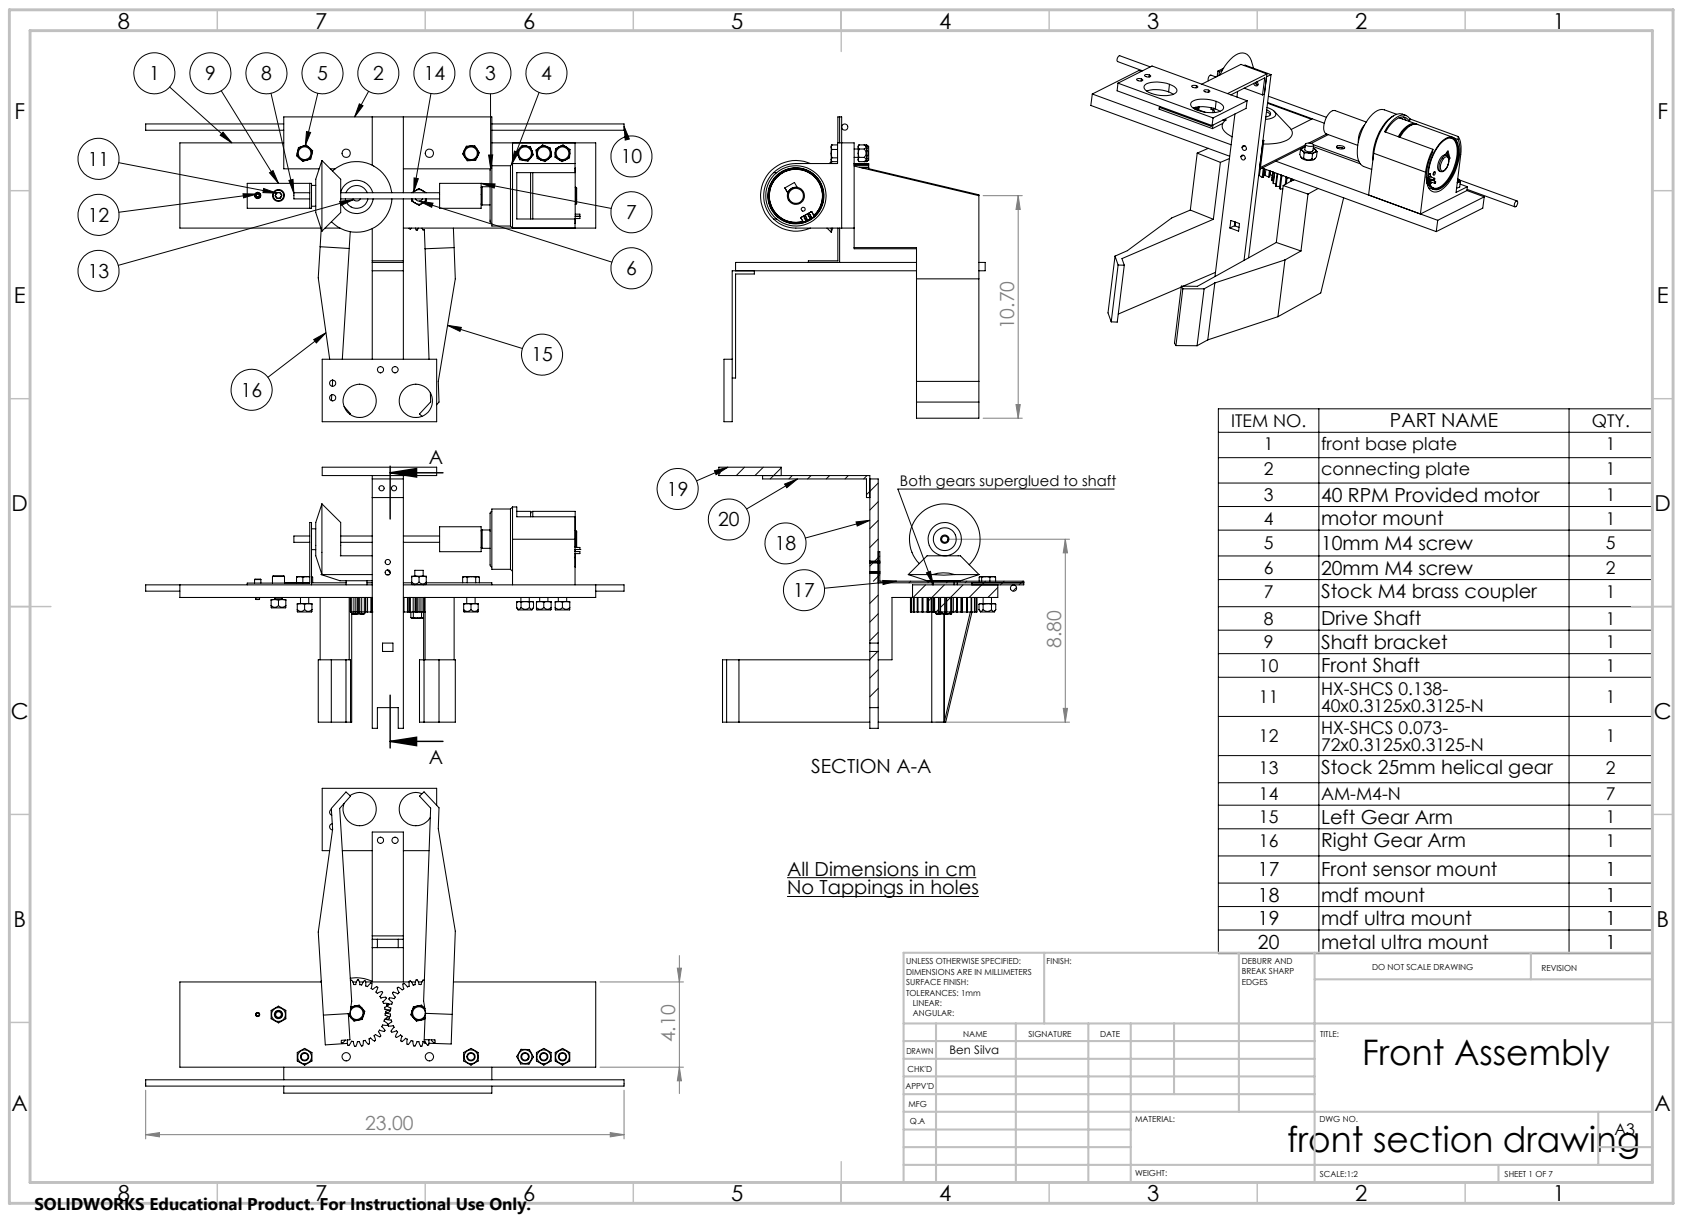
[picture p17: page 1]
SECTION A-A; Both gears superglued to shaft 19; SCALE:1:2; SHEET 1 OF 7

ITEM NO. | PART NAME | QTY.
1 | front base plate | 1
2 | connecting plate | 1
3 | 40 RPM Provided motor | 1
4 | motor mount | 1
5 | 10mm M4 screw | 5
6 | 20mm M4 screw | 2
7 | Stock M4 brass coupler | 1
8 | Drive Shaft | 1
9 | Shaft bracket | 1
10 | Front Shaft | 1
11 | HX-SHCS 0.138-40x0.3125x0.3125-N | 1
12 | HX-SHCS 0.073-72x0.3125x0.3125-N | 1
13 | Stock 25mm helical gear | 2
14 | AM-M4-N | 7
15 | Left Gear Arm | 1
16 | Right Gear Arm | 1
17 | Front sensor mount | 1
18 | mdf mount | 1
19 | mdf ultra mount | 1
20 | metal ultra mount | 1

All Dimensions in cm
No Tappings in holes

UNLESS OTHERWISE SPECIFIED: DIMENSIONS ARE IN MILLIMETERS SURFACE FINISH: TOLERANCES: 1mm LINEAR: ANGULAR: | FINISH: | DEBURR AND BREAK SHARP EDGES | DO NOT SCALE DRAWING | REVISION

DRAWN | | | | | | | Front Assembly Ben Silva

NAME | SIGNATURE | DATE | | | | TITLE:

CHK'D
APPV'D
MFG
Q.A | | | | MATERIAL: front section drawing | DWG NO. | A3

SOLIDWORKS Educational Product. For Instructional Use Only.

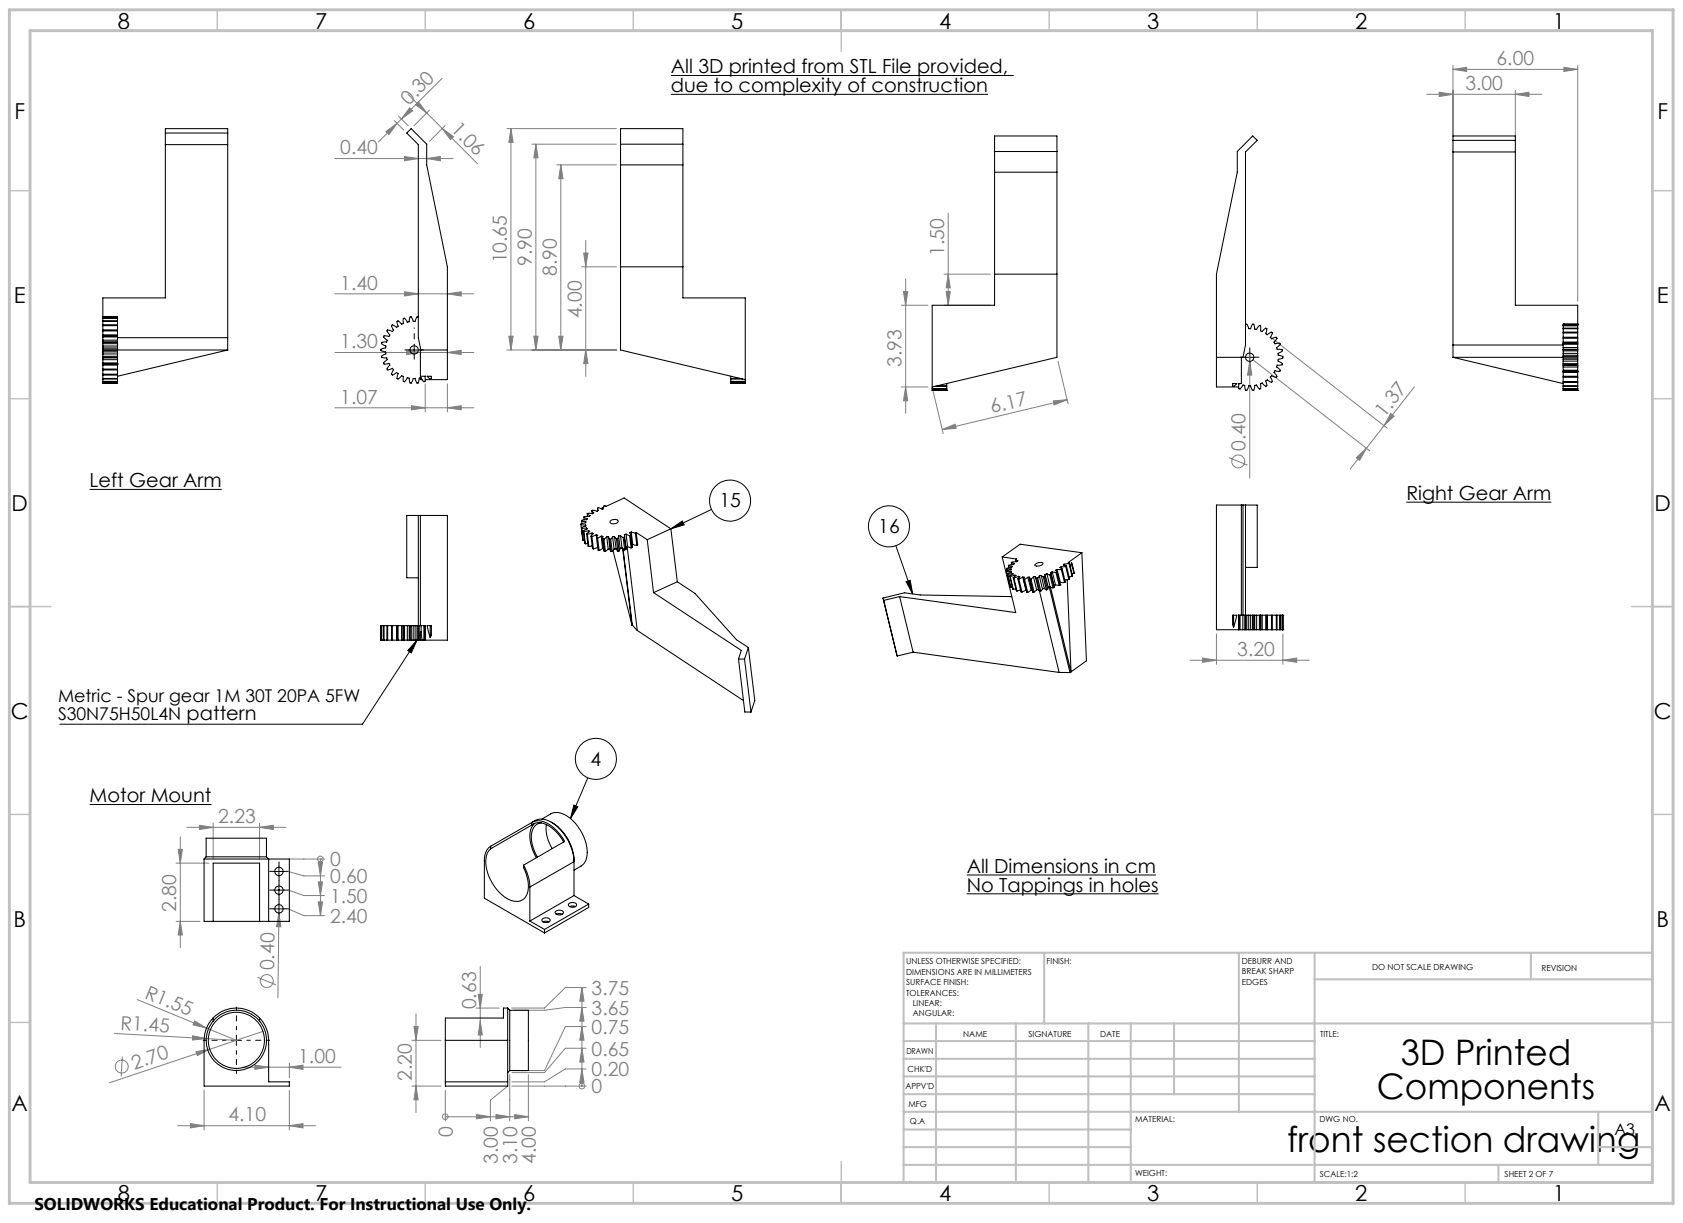
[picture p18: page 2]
Left Gear Arm; Right Gear Arm; Motor Mount; FINISH:; DEBURR AND; BREAK SHARP; DO NOT SCALE DRAWING; REVISION

All 3D printed from STL File provided,
due to complexity of construction

Metric - Spur gear 1M 30T 20PA 5FW
S30N75H50L4N pattern

All Dimensions in cm
No Tappings in holes

UNLESS OTHERWISE SPECIFIED:
DIMENSIONS ARE IN MILLIMETERS
SURFACE FINISH:
TOLERANCES:
LINEAR:
ANGULAR:

NAME | SIGNATURE | DATE | TITLE: 3D Printed Components

DRAWN
CHK'D
APPV'D
MFG

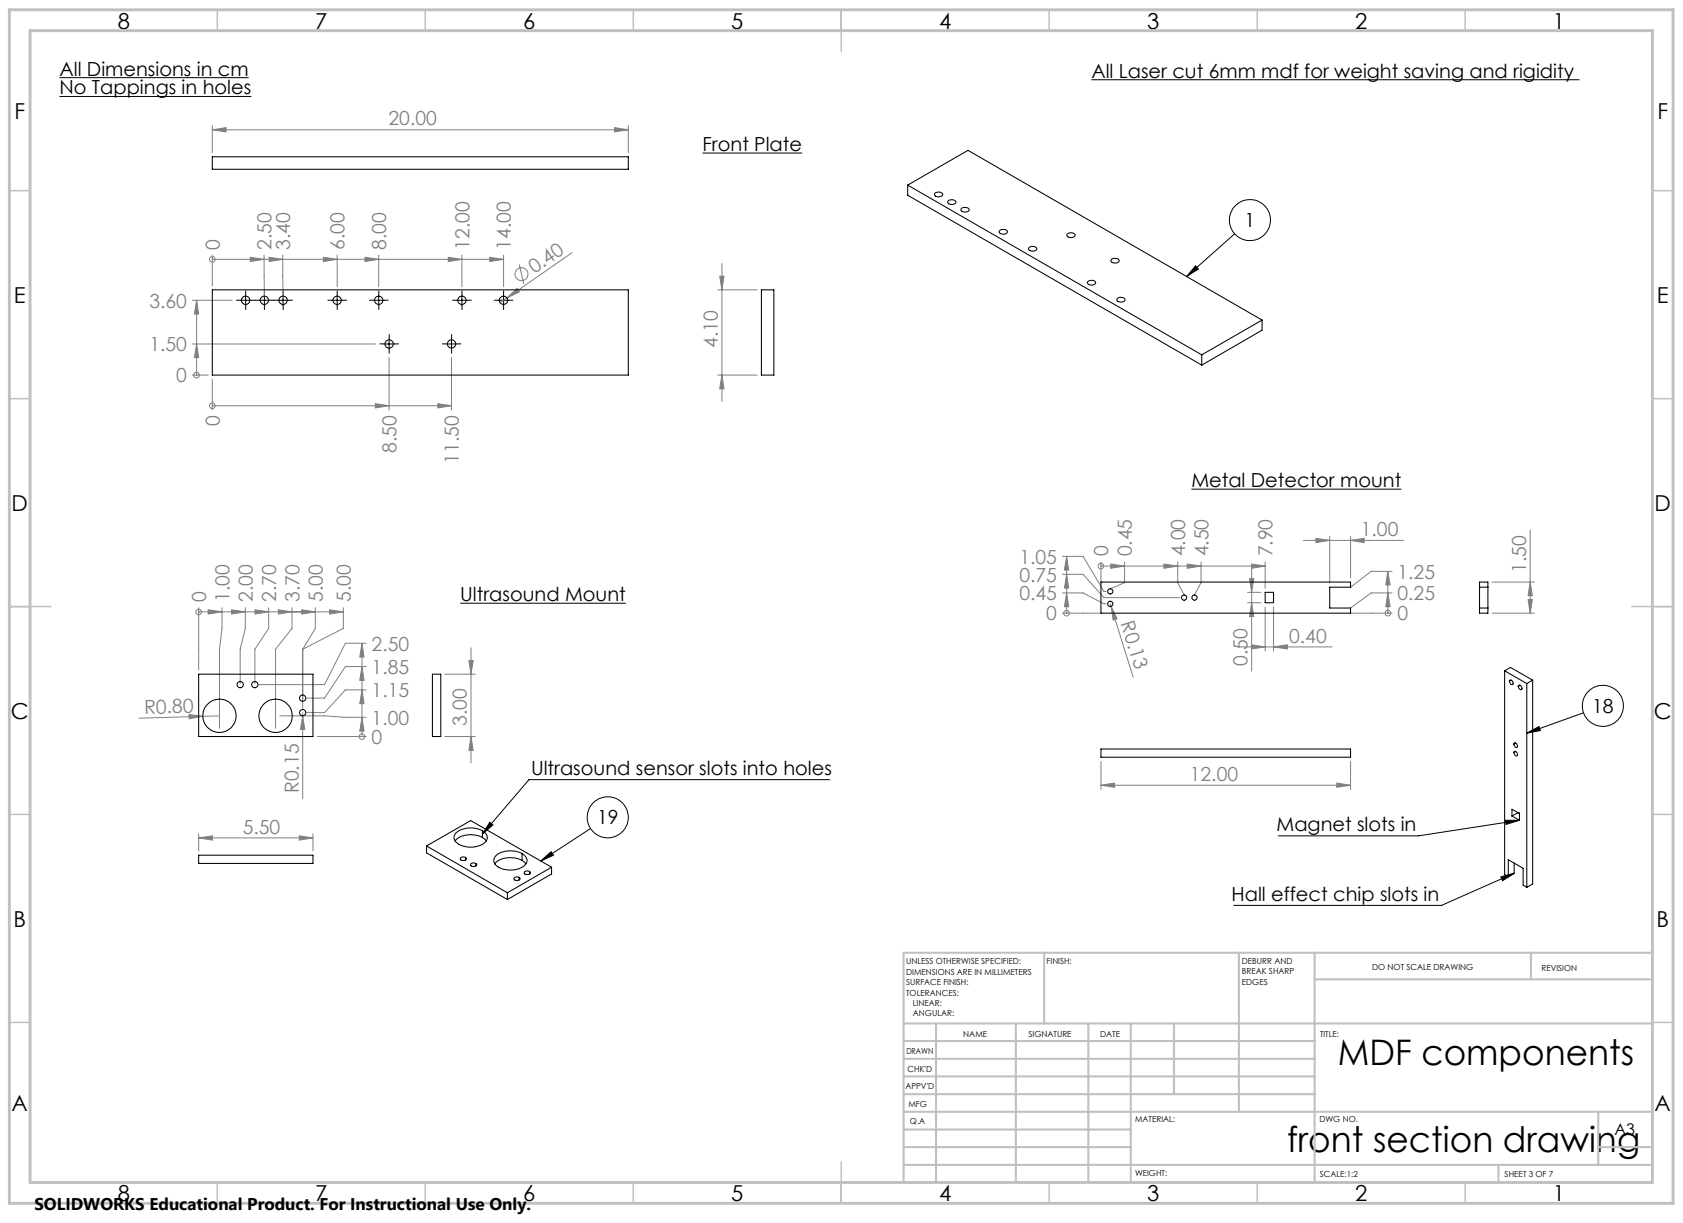
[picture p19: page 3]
All Dimensions in cm; All Laser cut 6mm mdf for weight saving and rigidity No Tappings in holes; Front Plate; Ultrasound Mount; FINISH:; DEBURR AND; BREAK SHARP; DO NOT SCALE DRAWING; REVISION

Metal Detector mount

Ultrasound sensor slots into holes

Magnet slots in

Hall effect chip slots in

UNLESS OTHERWISE SPECIFIED:
DIMENSIONS ARE IN MILLIMETERS
SURFACE FINISH:
TOLERANCES:
LINEAR:
ANGULAR:

NAME | SIGNATURE | DATE | TITLE: MDF components

DRAWN
CHK'D
APPV'D
MFG

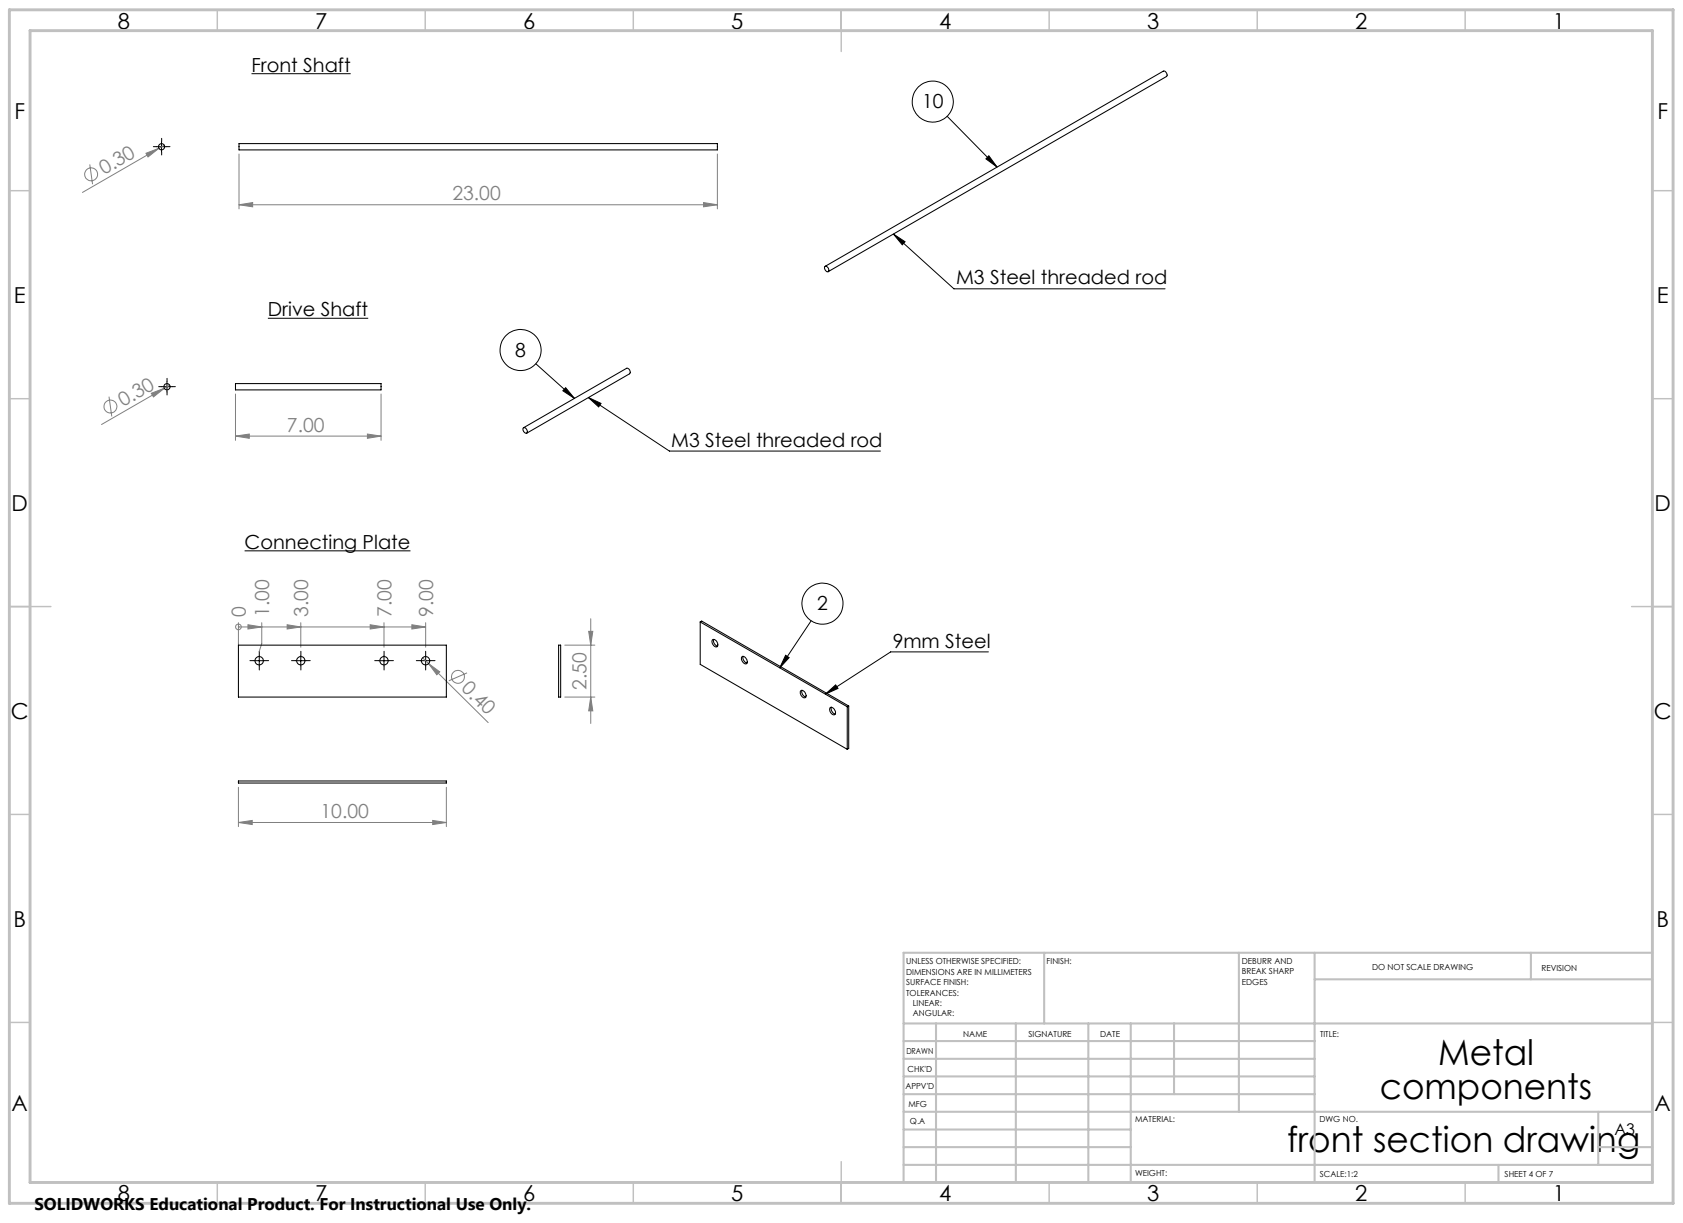
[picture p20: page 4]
9mm Steel; Front Shaft; Drive Shaft; Connecting Plate; FINISH:; DEBURR AND; BREAK SHARP; DO NOT SCALE DRAWING; REVISION

M3 Steel threaded rod

UNLESS OTHERWISE SPECIFIED:
DIMENSIONS ARE IN MILLIMETERS
SURFACE FINISH:
TOLERANCES:
LINEAR:
ANGULAR:

NAME | SIGNATURE | DATE | TITLE: Metal components

DRAWN
CHK'D
APPV'D
MFG

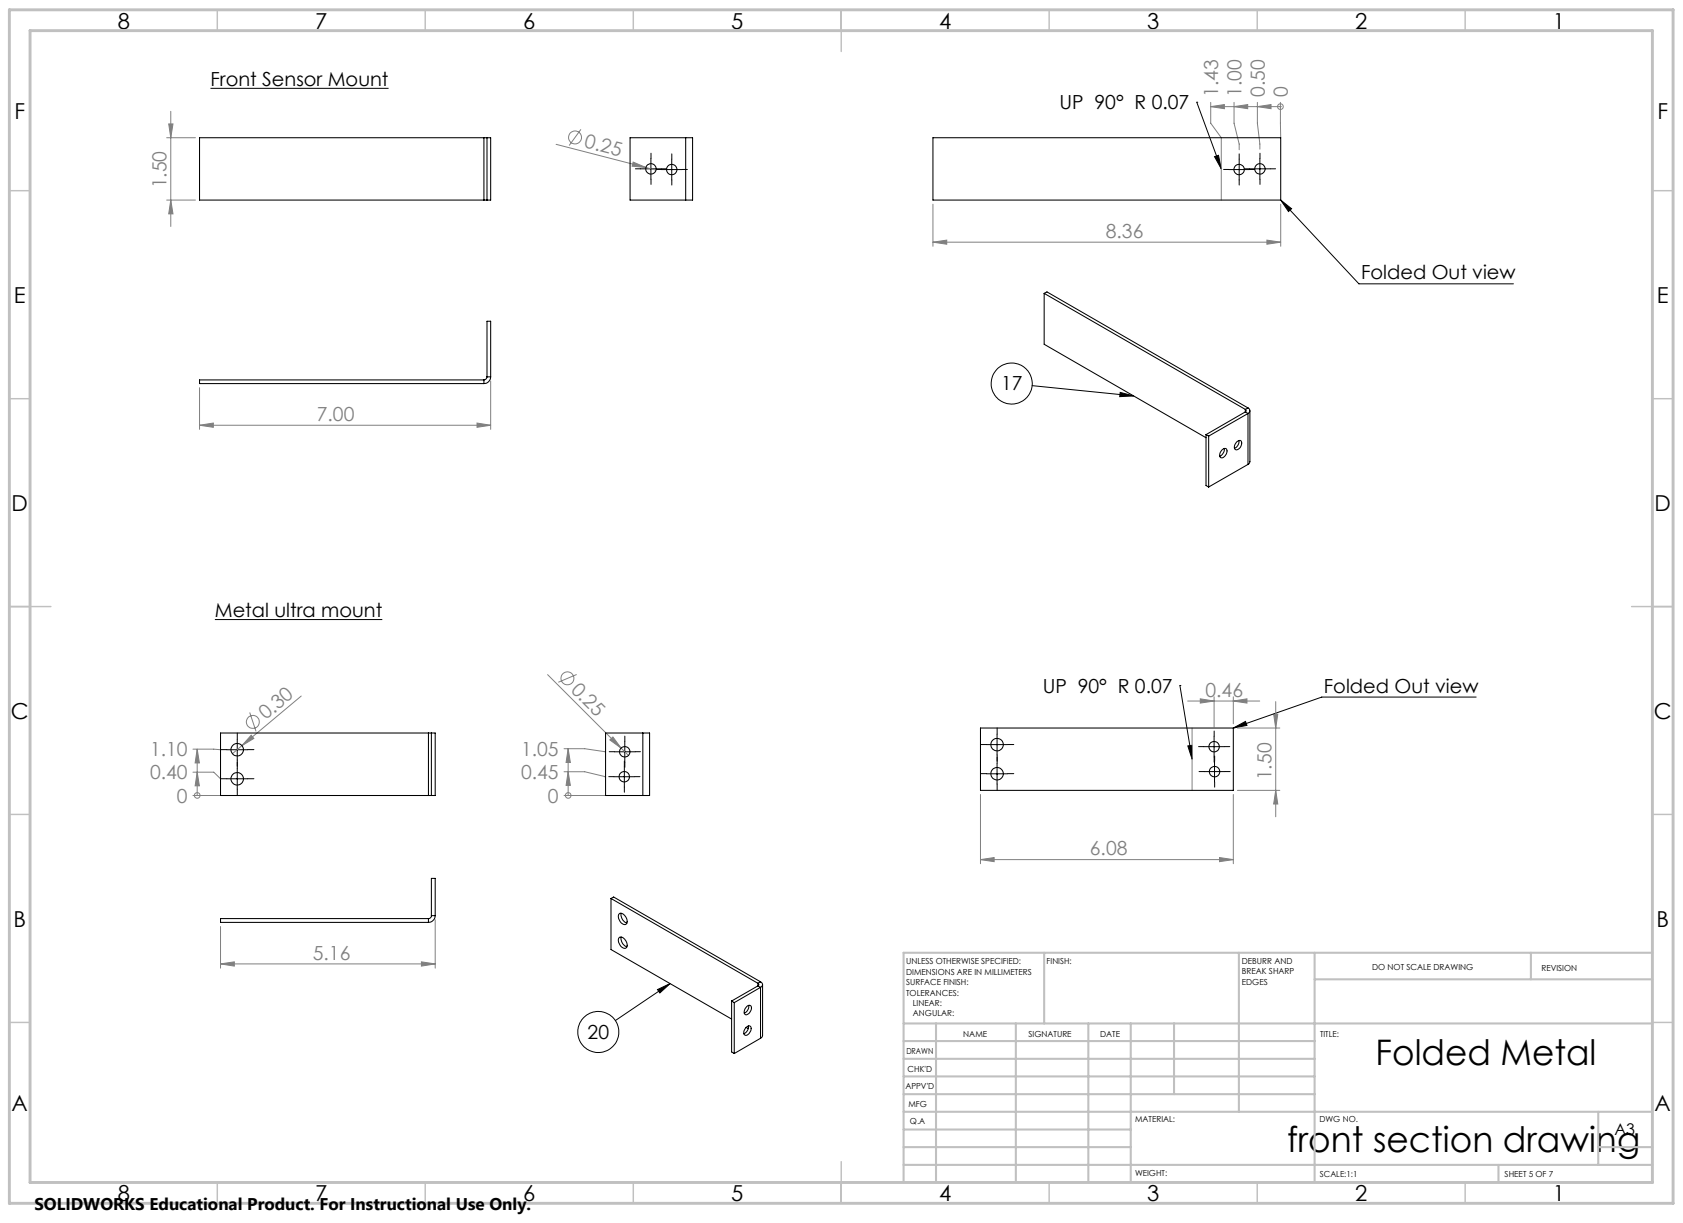
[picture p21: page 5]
Folded Out view; FINISH:; DEBURR AND; BREAK SHARP; DO NOT SCALE DRAWING; REVISION; SCALE:1:1; SHEET 5 OF 7

Front Sensor Mount

Folded Out view

Metal ultra mount

UNLESS OTHERWISE SPECIFIED:
DIMENSIONS ARE IN MILLIMETERS
SURFACE FINISH:
TOLERANCES:
LINEAR:
ANGULAR:

NAME | SIGNATURE | DATE | TITLE: Folded Metal

DRAWN
CHK'D
APPV'D
MFG

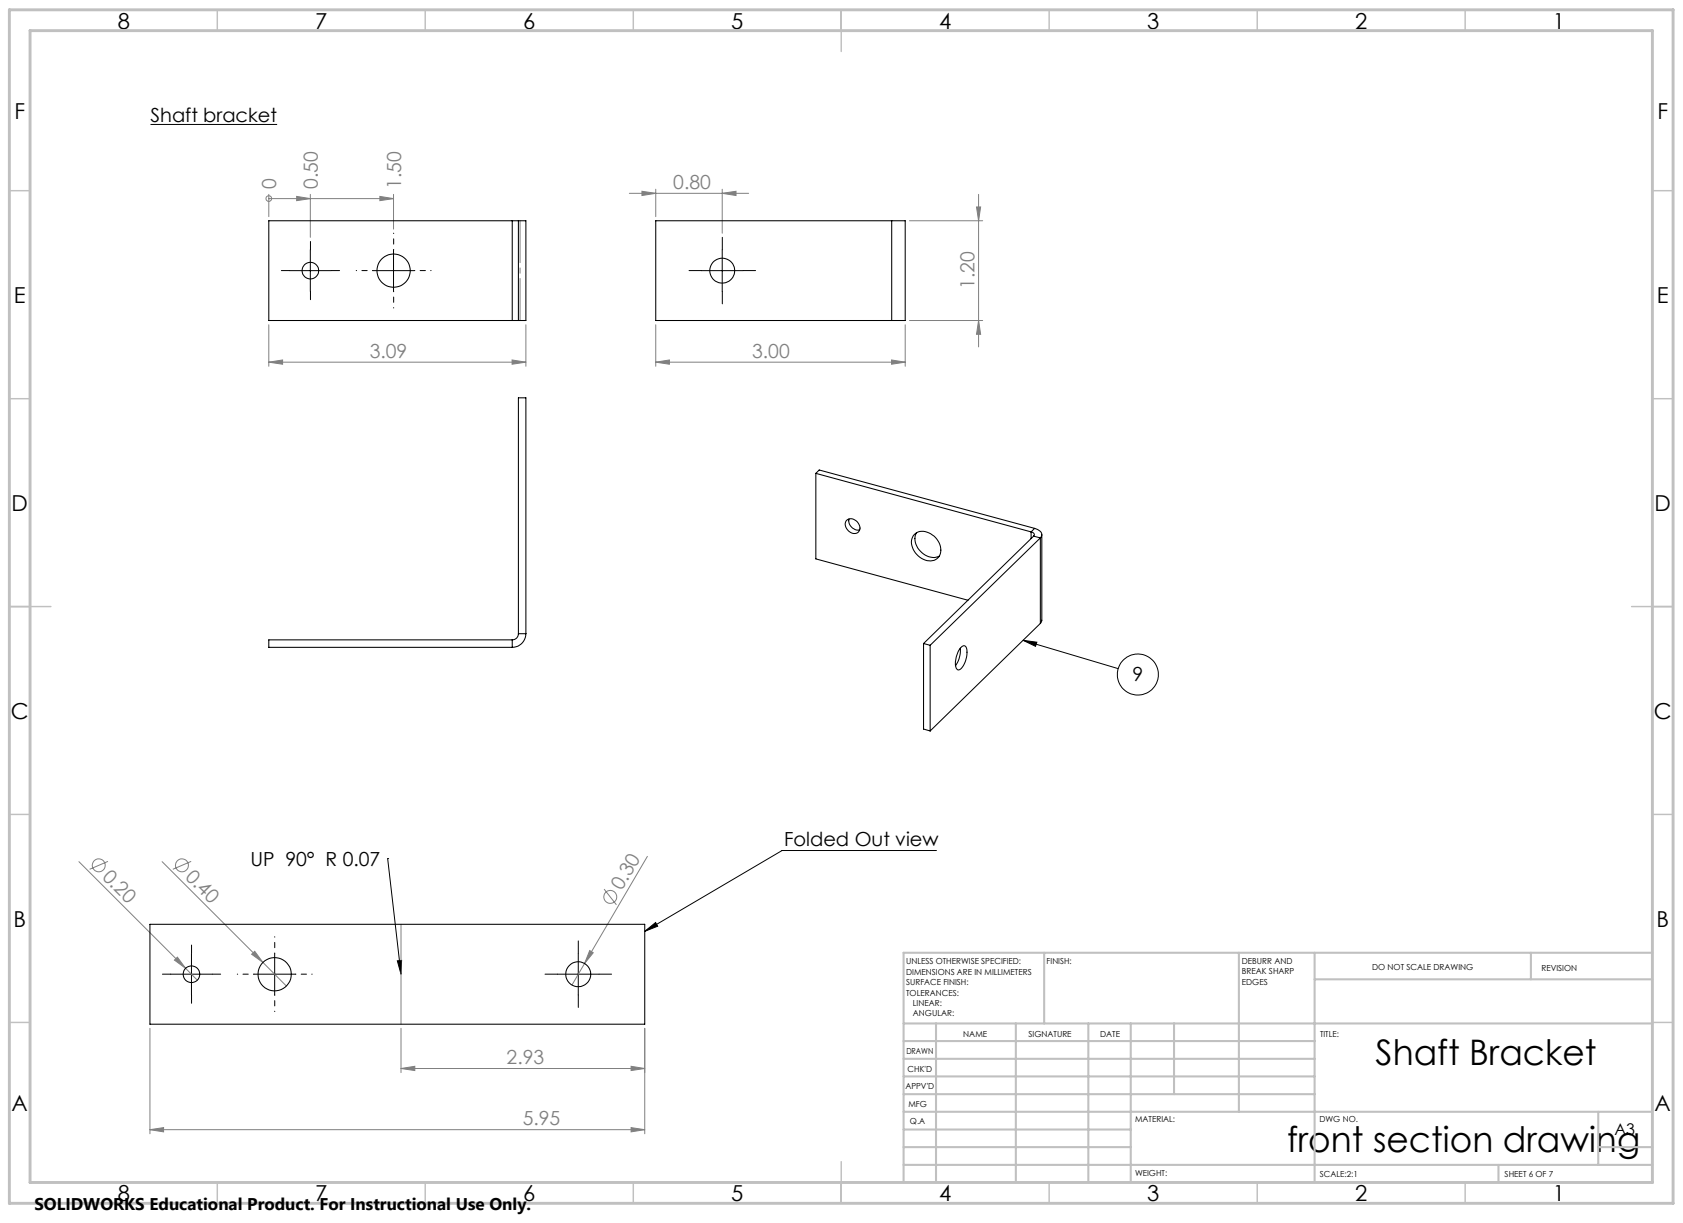
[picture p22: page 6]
Shaft bracket; FINISH:; DEBURR AND; BREAK SHARP; DO NOT SCALE DRAWING; REVISION; SCALE:2:1; SHEET 6 OF 7

Folded Out view

UNLESS OTHERWISE SPECIFIED:
DIMENSIONS ARE IN MILLIMETERS
SURFACE FINISH:
TOLERANCES:
LINEAR:
ANGULAR:

NAME | SIGNATURE | DATE | TITLE: Shaft Bracket

DRAWN
CHK'D
APPV'D
MFG

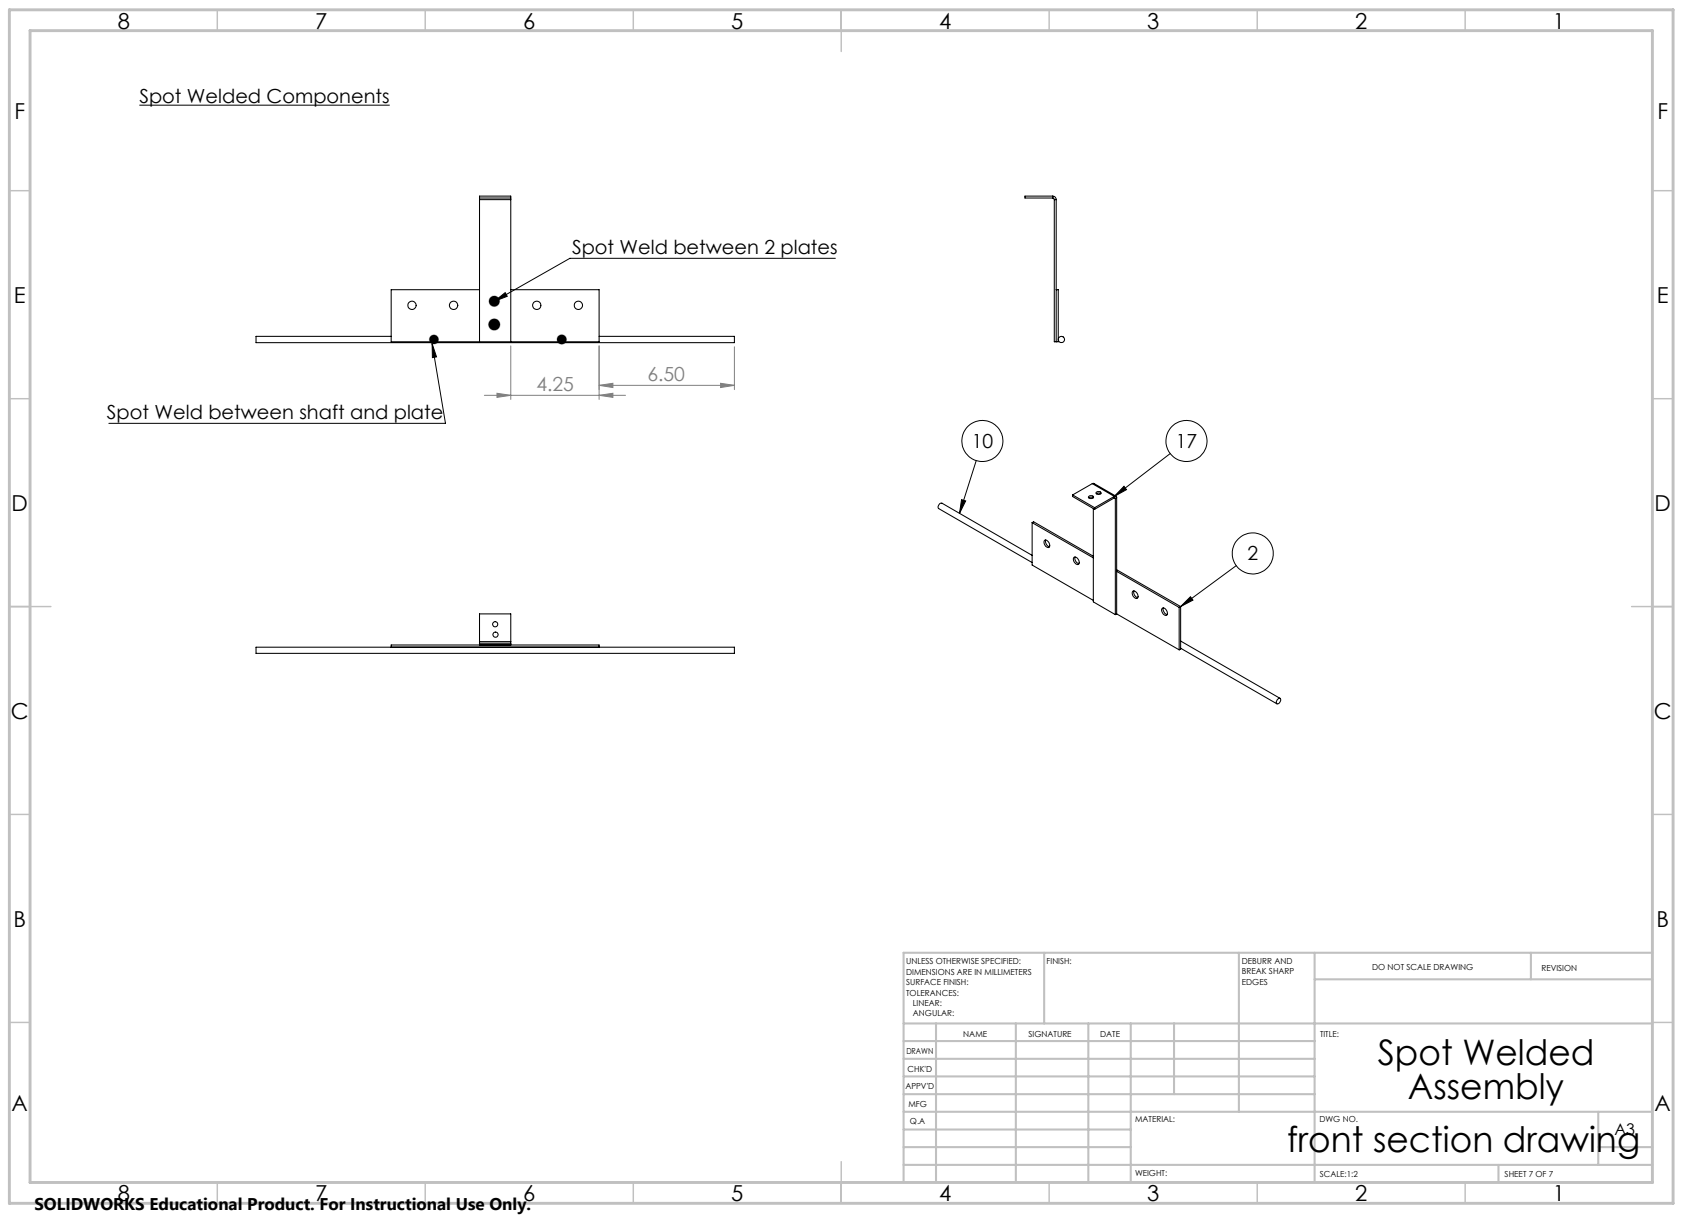
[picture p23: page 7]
FINISH:; DEBURR AND; BREAK SHARP; DO NOT SCALE DRAWING; REVISION

Spot Welded Components

Spot Weld between 2 plates

Spot Weld between shaft and plate

UNLESS OTHERWISE SPECIFIED:
DIMENSIONS ARE IN MILLIMETERS
SURFACE FINISH:
TOLERANCES:
LINEAR:
ANGULAR:

NAME | SIGNATURE | DATE | TITLE: Spot Welded Assembly

DRAWN
CHK'D
APPV'D
MFG

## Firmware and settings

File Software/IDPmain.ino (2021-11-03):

#include <RunningAverage.h>
#include <Wire.h>
#include <Adafruit_MotorShield.h>
#include "utility/Adafruit_MS_PWMServoDriver.h"
#include <Servo.h>
using namespace std;



// ___ OBJECTS ___
Adafruit_MotorShield AFMS = Adafruit_MotorShield();
Adafruit_DCMotor *leftMotor = AFMS.getMotor(3);
Adafruit_DCMotor *rightMotor = AFMS.getMotor(4);
Adafruit_DCMotor *grabberMotor = AFMS.getMotor(2);
Servo liftServo;



// ___ CONSTANTS ___
const int MOTOR_ACCEL = 1000;
const float SERVO_SPEED = 1;
const unsigned long FORWARD_10cm_TIME = 850; // test done
const unsigned long ROTATE_30_TIME = 580; //test done
const unsigned long SWEEP_TIME = 800;
#define leftLineSensor 7
#define rightLineSensor 11
#define ledRed 0
#define ledGreen 1
#define ledOrange 2
#define HallPin A0
#define SWPin 3


// ___ VARIABLE INITS ___
// LEDs
unsigned long ledActiveT = 0;

// Ultrasonic sensor
int trigPin = 12;    // Trigger
int echoPin = 13;    // Echo
long T_Gnd_min = 9.5;
long T_Block_max = 9.5;
// need to test value after fix ultrasonic


// Cache for the current motor speeds
// The caches are signed to signify forward or backward movement
int leftMotorCurrent = 0;
int rightMotorCurrent = 0;

// Cache for target velocities for the motor speeds
// These are used to allow smooth acceleration from the current motor speeds to the new ones
int leftMotorTarget = 0;
int rightMotorTarget = 0;


// Servo
float servoAngle = 0;
float servoAngleTarget = 150;


// Running average of sensor values, for more accurate read values
RunningAverage leftLineSensorRA(4);
RunningAverage rightLineSensorRA(4);
RunningAverage distSensorRA(4);
RunningAverage isBlockRA(4);

bool rightLineSensorPrev = false;
bool leftLineSensorPrev = false;

// When first detecting a line, detectedPerpendicularLine will tick true for one loop, then go back to false.
bool detectedPerpendicularLine = false;
bool onPerpendicularLine = false;

// State
enum State_enum {START, REACH_COLLECTION_POINT, STARTING_BLOCK_SEARCH, SWEEP, SWEEP_FORWARD, PICK_UP_BLOCK, RETURN_TO_LINE, TURN_AROUND, GO_TO_DROPOFF, PICKING_DROPOFF, DROPPING_BLOCK, FIND_START_LINE, TURNING_TO_START, RETURN_TO_START, END};
uint8_t state = START;             //uint8_t is an 8-bit integer / byte
unsigned long t = 0; // t is incremented after each loop.



// ___ FUNCTIONS ___



// ___ ULTRASONIC SENSOR ___
void Set_Ultrasonic() {
  pinMode(trigPin, OUTPUT);
  pinMode(echoPin, INPUT);
}


long GetDis_Ultrasonic() {
  long duration = 0, cm;
  // The sensor is triggered by a HIGH pulse of 10 or more microseconds.
  // Give a short LOW pulse beforehand to ensure a clean HIGH pulse:
  for (int m = 0; m < 5; m++) {
    digitalWrite(trigPin, LOW);
    delayMicroseconds(5);
    digitalWrite(trigPin, HIGH);
    delayMicroseconds(10);
    digitalWrite(trigPin, LOW);
    duration += pulseIn(echoPin, HIGH);
    delay(2);
  }
  // Read the signal from the sensor: a HIGH pulse whose
  // duration is the time (in microseconds) from the sending
  // of the ping to the reception of its echo off of an object.


  // Convert the time into a distance
  //cm = (duration/2) / 29.1+1;     // Divide by 29.1 or multiply by 0.0343
  duration /= 5;
  cm = (duration / 2) / 29.1;
  if (cm < 50) return (cm);
  return 50;
}


int detectIsBlock() { // Ground->0; Block->1
  long dis = GetDis_Ultrasonic();
  if (dis < T_Block_max) return 1;
  else if (dis > T_Gnd_min) return 0;
  else return 0;
}


bool getIsBlock() {
  return (isBlockRA.getAverage() > 0.5) ? true : false; // Return true if average is bigger than 0.5, else return false
}


// ___ SENSOR INTERFACE ___
void updateSensing() {
  leftLineSensorPrev = leftLineSensorVal();
  rightLineSensorPrev = rightLineSensorVal();
  leftLineSensorRA.addValue(digitalRead(leftLineSensor));
  rightLineSensorRA.addValue(digitalRead(rightLineSensor));
  //isBlockRA.addValue(detectIsBlock());

  updateLineDetection();
}


void updateLineDetection() {
  if (detectedPerpendicularLine) detectedPerpendicularLine = false;
  if (!onPerpendicularLine && leftLineSensorVal() && rightLineSensorVal()) detectedPerpendicularLine = true;

  onPerpendicularLine = leftLineSensorVal() && rightLineSensorVal();
}


bool leftLineSensorVal() {
  return (leftLineSensorRA.getAverage() > 0.5) ? true : false; // Return true if average is bigger than 0.5, else return false
}


bool rightLineSensorVal() {
  return (rightLineSensorRA.getAverage() > 0.5) ? true : false;
}


bool detectMetal() {
  RunningAverage RA(10);

  for (int i = 0; i < 10; i++) {
    RA.addValue(analogRead(HallPin));
    delay(5);
  }

  if (RA.getAverage() > 400)// Threshold // test
    return true;
  else return false;
}




// ___ MOTOR MANAGEMENT ___
void updateMotorSpeeds() {
  // Move the motorCurrent variables towards their target speeds
  if (leftMotorTarget > leftMotorCurrent) {
    leftMotorCurrent = min(leftMotorCurrent + MOTOR_ACCEL, leftMotorTarget);
  } else {
    leftMotorCurrent = max(leftMotorCurrent - MOTOR_ACCEL, leftMotorTarget);
  }

  if (rightMotorTarget > rightMotorCurrent) {
    rightMotorCurrent = min(rightMotorCurrent + MOTOR_ACCEL, rightMotorTarget);
  } else {
    rightMotorCurrent = max(rightMotorCurrent - MOTOR_ACCEL, rightMotorTarget);
  }
}


void setMotorSpeeds() {
  // Set motor speeds based on the motorCurrent values
  leftMotor->run( (leftMotorCurrent < 0) ? BACKWARD : (leftMotorCurrent > 0) ? FORWARD : RELEASE);
  leftMotor->setSpeed(abs(leftMotorCurrent));

  rightMotor->run( (rightMotorCurrent < 0) ? BACKWARD : (rightMotorCurrent > 0) ? FORWARD : RELEASE);
  rightMotor->setSpeed(abs(rightMotorCurrent));
}


void updateMotors() {
  // Call one-per-loop methods for motors
  updateMotorSpeeds();
  setMotorSpeeds();
  updateServo();
  
}



// ___ GRABBER ___
void updateServo() {
  //servoAngle = liftServo.read();
  if (servoAngleTarget > servoAngle) {
    servoAngle = min(servoAngle + SERVO_SPEED, servoAngleTarget);
  } else {
    servoAngle = max(servoAngle - SERVO_SPEED, servoAngleTarget);
  }
  liftServo.write(servoAngle);
}


void GrabberDown() {
  servoAngleTarget = 50;
}


void GrabberUp() {
  servoAngleTarget = 150;
}


void setGrabberClosed(bool closeState) {
  grabberMotor->run(closeState ?  FORWARD : BACKWARD );
  grabberMotor->setSpeed(255);

}



// ___ DRIVING INTERFACE ___
void setDriveDir(String dir) {
  // Set the direction for the robot to drive in
  // Takes a String parameter
  if (dir == "Stop") {
    leftMotorTarget = 0;
    rightMotorTarget = 0;
  }
  if (dir == "Forward") {
    leftMotorTarget = -255;
    rightMotorTarget = -255;
  }
  if (dir == "SlowForward") {
    leftMotorTarget = -180;
    rightMotorTarget = -180;
  }
  if (dir == "Backward") {
    leftMotorTarget = 255;
    rightMotorTarget = 255;
  }
  if (dir == "Left") {
    leftMotorTarget = 255;
    rightMotorTarget = -255;
  }
  if (dir == "Right") {
    leftMotorTarget = -255;
    rightMotorTarget = 255;
  }
  if (dir == "SlowLeft") {
    leftMotorTarget = 255;
    rightMotorTarget = -255;
  }
  if (dir == "SlowRight") {
    leftMotorTarget = -255;
    rightMotorTarget = 255;
  }
}



// ___ ALGORITHMS ___
void followLine() {
  if (onPerpendicularLine) setDriveDir("Forward");
  else if (!leftLineSensorVal() && !rightLineSensorVal()) setDriveDir("Forward");
  else if (leftLineSensorVal() && !rightLineSensorVal()) setDriveDir("Left");
  else if (!leftLineSensorVal() && rightLineSensorVal()) setDriveDir("Right");
}


bool returnToLine(bool leftOfLine) {
  setDriveDir(leftOfLine ? "SlowRight" : "SlowLeft");
  // Just stopped sensing line? (meaning it is now between the sensors)
  return (!rightLineSensorVal() && !leftLineSensorVal()) && (rightLineSensorPrev || leftLineSensorPrev);
}


// ___ MAIN ___
void setup() {
  // put your setup code here, to run once:
  AFMS.begin();
  liftServo.attach(9);  // attaches the servo on pin 9 to the servo object

  pinMode(leftLineSensor, INPUT);
  pinMode(rightLineSensor, INPUT);
  pinMode(HallPin, INPUT);
  pinMode(SWPin, INPUT);

  pinMode(ledRed, OUTPUT);
  pinMode(ledGreen, OUTPUT);
  pinMode(ledOrange, OUTPUT);
  Set_Ultrasonic();
  //Serial.begin(9600);

  setGrabberClosed(true);

  delay(1000);

  servoAngle = liftServo.read();
  while(servoAngle != servoAngleTarget) {
  updateServo();
  delay(10);
  }

  while(!digitalRead(SWPin)); // wait until swPin reads HIGH




}


void loop() {
  // Logic
  static int counter = 0;
  static unsigned long timer = 0;
  // To remember what the currently held block's type is
  static bool isBlockMetal = false;
  // When scanning off the line, this lets the robot know which side of the line it's on.
  static bool leftOfLine = true;
  static int blockNum = 0;
  



  switch (state) {

    case START: // Travel from start to pickup box
      setGrabberClosed(false);
      followLine();
      if (detectedPerpendicularLine) counter = counter + 1;
      if (counter == 2) {
        counter = 0;
        state = REACH_COLLECTION_POINT;
        if (blockNum == 0) timer = t + 14000; // test done
        else timer = t + 12500; // test done
      }


    break;


    case REACH_COLLECTION_POINT:
      if (t < timer) followLine(); // keep moving with grabber up
      else {
        followLine();
        GrabberDown();
        if (detectedPerpendicularLine)
        {
          timer = t + 1 * FORWARD_10cm_TIME ; // 0cm // test
          if (blockNum == 0) {
            state = PICK_UP_BLOCK;
          } else {
            state = STARTING_BLOCK_SEARCH;
          }
        }
      }

      break;


    case STARTING_BLOCK_SEARCH:
      if (t < timer) setDriveDir("Forward");
      else {
        state = SWEEP;  // sweep time // test
        leftOfLine = true;
        timer = t +  SWEEP_TIME;
      }
      break;

    case SWEEP:
      if (t < timer) { // Turning away from line
        setDriveDir(leftOfLine ? "SlowLeft" : "SlowRight");
      }
      else if (returnToLine(leftOfLine)) { // Returned back to line?
        if (leftOfLine) { // Returning from left
          timer = t + SWEEP_TIME;  // sweep time // test
        }
        else { // Returning from right
          state = SWEEP_FORWARD;
          timer = t + FORWARD_10cm_TIME;  // time moving forward
        }
        leftOfLine = !leftOfLine;
      }

      //else if (detectIsBlock() == 1) { // <else if] -> <if>

        state = PICK_UP_BLOCK;
        timer = t + 0;
      }
      break;

    case SWEEP_FORWARD:
      if (t < timer) setDriveDir("Forward");
      else {
        state = SWEEP;
        timer = t + SWEEP_TIME; // sweep time // test
        leftOfLine = true;
      }
      break;

    case PICK_UP_BLOCK:
      // TODO identify
      if (t < timer) setDriveDir("SlowForward");
      else {
        setDriveDir("Stop");
        isBlockMetal = detectMetal();
        ledActiveT = t + 8000;
        
        setGrabberClosed(true);
        timer = t + 2000; // test
        state = RETURN_TO_LINE;
      }
      break;

    case RETURN_TO_LINE:
      if (t < timer);
      else { 
        GrabberUp();
        if (returnToLine(leftOfLine) || (blockNum == 0)) {
          state = TURN_AROUND;
          timer = t + ROTATE_30_TIME * 4; // Time to skip lines // test
        }
      }

      break;

    case TURN_AROUND:
      if (returnToLine(false) && t > timer) {
        
        state = GO_TO_DROPOFF;
        counter = 0;
      }
      break;

    case GO_TO_DROPOFF:
      if (t < timer) setDriveDir("Forward");
      else if (counter == 1) {
        state = PICKING_DROPOFF;
        timer = t + ROTATE_30_TIME * 3;
      } else {
        followLine();
        if (detectedPerpendicularLine) {
          timer = t + FORWARD_10cm_TIME;
          counter = 1;
        }
      }
      break;

    case PICKING_DROPOFF:
      if (t < timer) setDriveDir(isBlockMetal ? "Right" : "Left");
      else {
        blockNum = blockNum + 1;
        state = DROPPING_BLOCK;
        timer = t + 1000; // test
      }
      break;

    case DROPPING_BLOCK:
      setDriveDir("Stop");
      setGrabberClosed(false);
      GrabberUp();
      if (t > timer) {
        state = TURNING_TO_START;
        timer = t + ROTATE_30_TIME * 2.5; // test done
      }
      break;

    case FIND_START_LINE:
      if (returnToLine(isBlockMetal) && t > timer) {
        state = REACH_COLLECTION_POINT;
      }
      break;

    case TURNING_TO_START:
      if (returnToLine(!isBlockMetal) && t > timer) {
        state = RETURN_TO_START;
        counter = 0;
      }
      break;

    case RETURN_TO_START:
      
      if (counter == 1) {
        setDriveDir("Forward");
        if (t > timer) state = END;
      }
      else {
        followLine();
        
        if (detectedPerpendicularLine) {
          timer = t + FORWARD_10cm_TIME * 2;
          counter = 1; 
        }
      }

      case END:
        setDriveDir("Stop");
        GrabberUp();
        setGrabberClosed(false);
      break;

  }


  // LED
  digitalWrite(ledOrange, ((t % 500) < 250) && (leftMotorCurrent != 0 || rightMotorCurrent != 0) ? HIGH : LOW);
  digitalWrite((isBlockMetal) ? ledRed : ledGreen, (t < ledActiveT) ? HIGH : LOW);

  // Loop updates
  updateMotors();
  updateSensing();

  /*
    if((millis()-t)>8) digitalWrite(ledRed,HIGH);
    else digitalWrite(ledRed,LOW);
  */

  //while((unsigned long)(millis() - t) <= 10){ // actual period ~7
  // wait here
  //}
  t = millis();
}

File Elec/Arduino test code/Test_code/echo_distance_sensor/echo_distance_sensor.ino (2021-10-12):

int trigPin = 11;    // Trigger
int echoPin = 12;    // Echo
long duration, cm, inches;
 
void setup() {
  //Serial Port begin
  Serial.begin (9600);
  //Define inputs and outputs
  pinMode(trigPin, OUTPUT);
  pinMode(echoPin, INPUT);
}
 
void loop() {
  // The sensor is triggered by a HIGH pulse of 10 or more microseconds.
  // Give a short LOW pulse beforehand to ensure a clean HIGH pulse:
  digitalWrite(trigPin, LOW);
  delayMicroseconds(5);
  digitalWrite(trigPin, HIGH);
  delayMicroseconds(10);
  digitalWrite(trigPin, LOW);
 
  // Read the signal from the sensor: a HIGH pulse whose
  // duration is the time (in microseconds) from the sending
  // of the ping to the reception of its echo off of an object.
  pinMode(echoPin, INPUT);
  duration = pulseIn(echoPin, HIGH);
 
  // Convert the time into a distance
  cm = (duration/2) / 29.1;     // Divide by 29.1 or multiply by 0.0343
  inches = (duration/2) / 74;   // Divide by 74 or multiply by 0.0135


  Serial.print(duration);
  //Serial.print(inches);
  Serial.print("in, ");
  Serial.print(cm);
  Serial.print("cm");
  Serial.println();
  
  delay(250);
}

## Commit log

2021-10-11 Update Gantt Chart
    [Gantt Chart 20211009.xlsx, Gantt Chart.xlsx]
2021-10-11 Clean up folder
    [Gantt Chart.xlsx, Schematic diagram.fzz]
2021-10-12 Line sensor + echo distance sensor
    [Circuit diagram.fzz]
2021-10-12 Gantt Chart
    [Gantt Chart.xlsx]
2021-10-14 Small motor function fix, and suggestion
    [IDPmain.ino]
2021-10-14 1st report
    [Gantt Chart.xlsx]
2021-10-16 Revamped driving code and cleaned code
    Still need to add rolling averages for sensors
2021-10-16 Update Gantt Chart.xlsx
    [Gantt Chart.xlsx]
2021-10-18 Add sensor logic
2021-10-19 Line sensor library
2021-11-02 Add LEDs
2021-11-02 LED stuff
2022-09-06 summarise IDP
    [Circuit diagram.fzz, Gear Drive.SLDASM, Schematic diagram.fzz]
